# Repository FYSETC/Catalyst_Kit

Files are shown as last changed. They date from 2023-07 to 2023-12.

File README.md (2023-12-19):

# Introduction

 This is a kit for the VORON 0.2. FYSETC Voron 0. 2 Pro R1 Kit.

# Feature 

The new **Voron 0. 2 Pro R1 Kit** has a new design for the electronic part, which is easier to connect and configure, and is as close as possible to out-of-the-box use.

# BOM

[Voron 0.2 R1 Pro](https://github.com/FYSETC/FYSETC-Voron-0.2/blob/main/0.2%20R1/BOM.md)

# STL changes

### Additional STLs

Check it [here](https://github.com/FYSETC/FYSETC-Voron-0.2-Pro/tree/main/0.2%20R1/STL/ADD).

### Hotend Mount

Check it [here](https://github.com/FYSETC/FYSETC-Voron-0.2-Pro/blob/main/0.2%20R1/STL/Toolheads/Hotend_Mounts/Fan_Saver/%5Ba%5D_FS_Hotend_Mount_Dragon.stl)

### Unnecessary STLs
- Rear_Bed_Mount_Right_x1.stl
- Front_Bed_Mount_x1.stl
- Rear_Bed_Mount_Left_x1.stl
- Drag_Chain_Spacer_x1.stl
- PCB_DIN_Clip_x2.stl
- PCB_DIN_Clip_x2.stl
- Fan_Mount_Bottom_x1.stl
- VHB_DIN_Mount.STL
- VHB_DIN_Mount.STL
- Fan_Mount_Top_x1.stl
- M2_Nut_Adapter_Rotated_x5.stl

# Wiring

### R1 Pro kit

Following is our Catalyst board wiring diagram for VORON 0.2 R1 pro kit.



# Installation Guide 

### Page 190 "ELECTRONICS & WIRING"

Following the Catalyst board wiring diagram for VORON 0.2 pro R1 kit.

Check it [here](https://github.com/FYSETC/FYSETC-Voron-0.2-Pro/blob/main/0.2%20R1/Fysetc%20Voron%20V0.2%20R1%20umbilical%20Wiring.pdf).

# Firmware&OS

## CM68 OS 

<p style="color: green">
<strong>
The control board of this kit has been installed with Klipper OS and MCU Klipper firmware at the factory. And it's pre-configured.
As long as the wiring is correct, it can be used after power on.
</strong>
</p>

<p style="color: red">
<strong>
Do not perform the following steps unless you are sure you want to reinstall the firmware.
</strong>
</p>

The control board uses the CM68 core based on RK3568 as the upper computer of Klipper. Its system is compiled based on Debian 10, and the environment and plug-ins required by Klipper are pre-installed. After burning, it can be used directly.

In general, the pre-installed system can be used directly without re-flashing, unless you encounter unsolvable program problems.

The OS of CM68 (voron-02-pro):

1. Install klipper and its necessary plug-ins in the initial version (Debian10):</br>
file name: rk3568-debian10-voron02pro-mainsail.rar</br>
Download：</br>
https://drive.google.com/file/d/13Tcclv2N4jrMm01r_HPVqZ3v6CVUCk1H/view?usp=drive_link

2. bugfix (Debian10) Install klipper and its necessary plug-ins:</br>
file name: cm68-debian10-voron02pro-mainsail-20230923-154632.img</br>
Fix "vdd_cpu: ramp_delay not set" warning</br>
Download：</br>
https://drive.google.com/file/d/13Tcclv2N4jrMm01r_HPVqZ3v6CVUCk1H/view?usp=drive_link

3. 5.1 kernel, Debian11, install klipper and its necessary plug-ins:</br>
file name: cm68-debian11-voron02pro-part-20231107-1211.img</br>
Download：</br>
https://drive.google.com/file/d/1rhYSTQhsnIySWOnArb-KzfS_5ioayIdm/view?usp=drive_link</br>

4. 5.1 kernel, Debian11, install all plug-ins supported by kiauh.</br>
**file name:** cm68-debian11-voron02pro-all-20231107-1157.img</br>
**Download:** </br>
https://drive.google.com/file/d/1RwSsYh74uzc6N8ZZUWCPG4JZDjomelVW/view?usp=drive_link
Google Docs

**5 & 6 Fixed the RTL8188EUS WIFI Diver issue** </br>

5. 5.1 kernel, Debian11, install all plug-ins supported by kiauh.</br>
**file name:** cm68-debian11-voron02pro-all-20231215.rar</br>
**Download:** </br>
https://drive.google.com/file/d/1aGxkKDje69fH9lJNZlRNIsSG2d_Z3Y20/view?usp=drive_link/</br>

6. 5.1 kernel, Debian11, install klipper and its necessary plug-ins:</br>
**file name:** cm68-debian11-voron02pro-part-20231215.rar</br>
**Download:** </br>
https://drive.google.com/file/d/1jtd5bbeK2osySYbc_Y-N9HqvL0vuzt-D/view?usp=drive_link/</br>

Update steps:

1. plugin the USB3.0 A-A cable into the interface on the upper layer of the blue USB3.0 socket,
2. open the "RKDevTool_Release",
3. hold the recovery button, click the reset button, when the RKDevTool found device, release the 2 buttons
4. Click the Upgrade Firmware tab, click the Firmware button to select the firmware, and click the Upgrade button to upgrade
5. Wait for the upgrade to complete. Remember not to cut off the power or unplug the data cable during the process, otherwise the upgrade will fail or even damage the CM68.

## MCU Firmware

<p style="color: red">
<strong>
Do not perform the following steps unless you are sure you want to reinstall the firmware.
</strong>
</p>

If you know the structure of Klipper, then you should understand that the firmware of the MCU is compiled and installed by the host computer (CM68). This is the way we recommend.

Of course, you can also use other methods to burn the MCU, such as through the "STM32CubeProgrammer" on the computer, or with the help of burning tools such as STlink. These need to be studied by yourself, and our control board also provides corresponding interfaces.

The MCU model we use is STM32F401RCT6, with an external 8Mhz crystal oscillator, and uses PA11/PA12 as USB communication. The following is the MCU configuration and burning process:

1. MCU enters DFU mode:

   - Powered off the whole machine
   - Use a jumper cap to connect 3V3 and B0(boot0)
   
  
   - Power on the whole machine and wait for it to start

2. Use putty or similar SSH tools to connect to CM68 using IP or host name

    ```
    host name: voron-02-pro.local
    Username: linaro
    Password: linaro
    If you are not very familiar with linux, do not use the root user to log in. Misoperation may cause damage to the system.
    Username: root
    Password: root
    ```

3. Configure the firmware:

    - use "lsusb" to ensure the mcu enter dfu mode,

       ```
       lsusb
       ```

    - configure the firmware
    
       ```
       cd ~/klipper
       make clean
       make menuconfig
       ```

4. update the firmware and reboot

    - Compile and burn the firmware:
    
      ```
       make flash FLASH_DEVICE=0483:df11
      ```
    
    - Powered off the whole machine
    - Use a jumper cap to connect B0(boot0) and G(GND)
      

    - Power on the whole machine and wait for it to start

# Print

## Connect via Ethernet

The control board defaults to obtain IP automatically, make sure your router can provide DHCP service normally. You only need to plug in the Internet cable, and when you see the green and yellow lights on, indicates that it is connected to the network.

You have two methods to login the mainsail webpage:

### IP address
you need to go to your router to find the device named voron-02-pro, and write down the IP address
### Host name
The kit has already installed the required plug-ins, and you can access the mainsail page through the pre-set host name: voron-02-pro.local

## Connect via WiFi

- First connect the machine to your LAN via Ethernet, make sure you can log in to CM68 via SSH.
- Plug the included USB wifi into any USB interface on CATALYST board
- Use the following command checks whether the wifi module is recognized:
```
sudo ifconfig
```
- Use the following command to connect to wifi
```
sudo wifi_sta_start.sh ssid password
```
- Use the following command checks whether the wifi module is connected to your router, and get the ip address:
```
sudo ifconfig
```

# FAQ

## 1. Can't find mcu/unable to connect to mcu
Reason:
       It may be that the status of boot0 is uncertain, causing the STM32 to enter the DFU mode, resulting in the connection error.
Solution:
   - Powered off the whole machine
   - Use a jumper cap to connect B0(boot0) and G(GND)
   - Power on the whole machine and wait for it to start
## 2. Mcu firmware version too low
Reason:
The factory version of the Klipper host is the same as that of the MCU. Maybe you have clicked the update button on the mainsail webpage to update the Klipper host. As a result, the version of the host is newer than the firmware of the MCU.
Solution:
update the mcu firmware: Refer to the Firmware&OS==>MCU Firmware
## 3. Temperature error
Reason:
You may have forgotten to connect the MX3.0 16P cable, or it may not be connected firmly.
Solution:
Make sure the MX3.0 16P cable is connected and secure.
## 4. How to use the accelerometer
Refer to Klipper document: 
https://www.klipper3d.org/Resonance_Compensation.html

## 5. Wifi Connection Issues
If you are having problems with your Catalyst wifi, please fix using the following solution. 

SSH into the Catalyst, and run the following command `sudo nano /etc/network/interfaces`

Once you have run the command, add the following lines 

```
auto wlan0
iface wlan0 inet dhcp
wpa-ssid Your Network Name Here
wpa-psk Your Password Goes Here
```
example if your wifi name is fysetcwifi and password was ItRocks:
```
auto wlan0
iface wlan0 inet dhcp
wpa-ssid fysetcwifi
wpa-psk ItRocks
```

# Support
Voron community: 
https://discord.gg/voron
FYSETC Facebook group: 
https://www.facebook.com/groups/238970713918171
FYSETC Discord:
https://discord.gg/T3XcJPgr 
# Buy Link
https://www.aliexpress.us/item/3256805148633512.html

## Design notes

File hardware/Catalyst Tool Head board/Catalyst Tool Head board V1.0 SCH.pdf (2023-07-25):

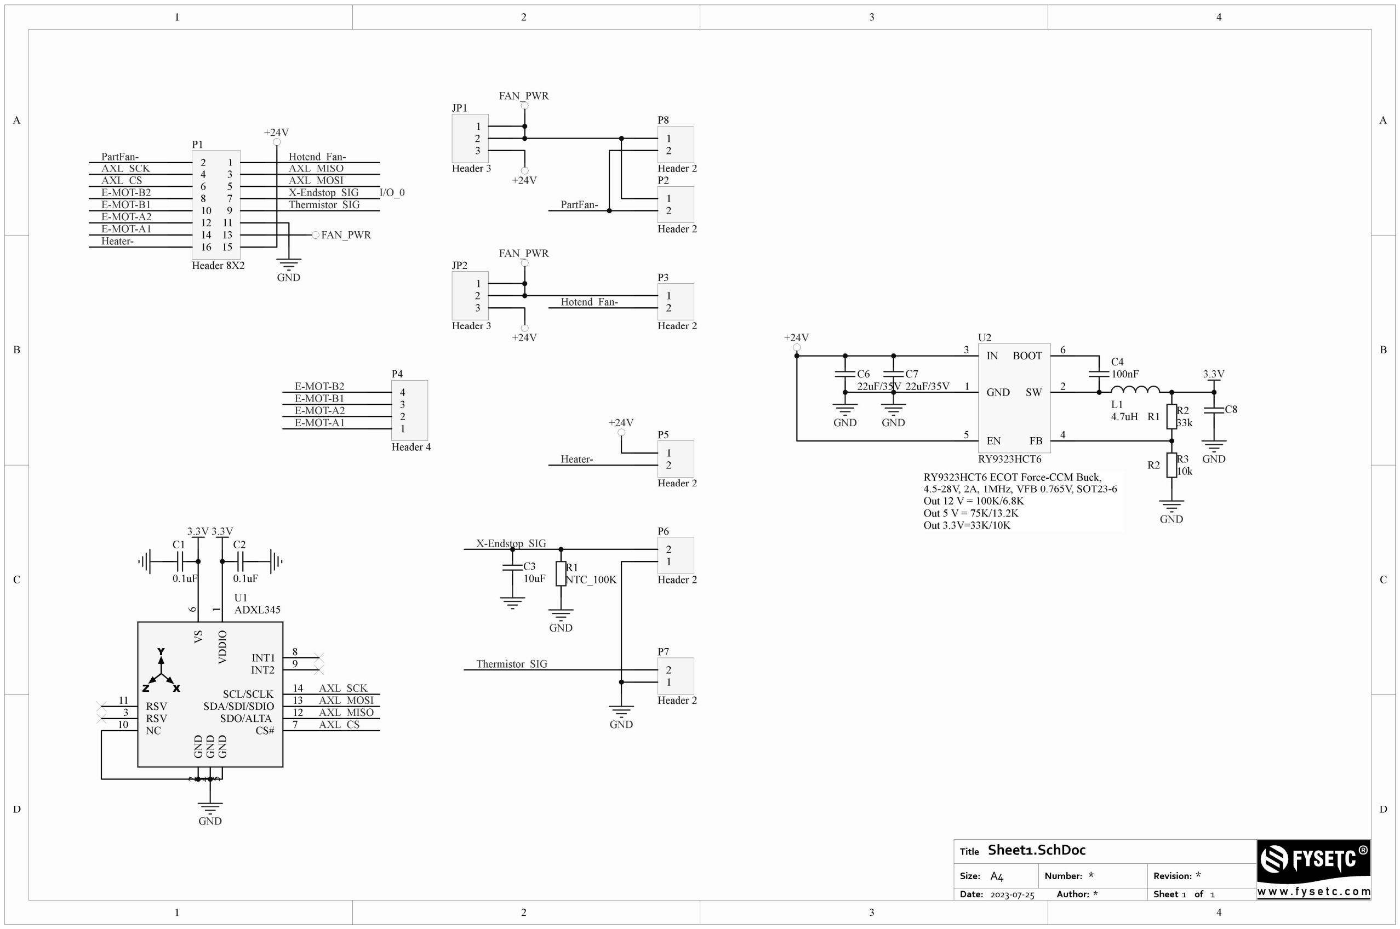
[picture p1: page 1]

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
## Sheet1.SchDoc

* | *
2023-07-25 | *

Title

Size: | Number:
Date:

Revision:
Author: | Sheet | of

A4

E-MOT-A1

E-MOT-A2

E-MOT-B1

E-MOT-B2
Thermistor_SIG

GND

+24V

Heater-

PartFan- | Hotend_Fan-
X-Endstop_SIG | I/O_0

AXL_MISO
AXL_CS | AXL_MOSI
AXL_SCK | 2 | 1
4 3
6 5
8 7
10 9
12 11
14 13
16 15

P1

Header 8X2

1

2

3

4

P4

Header 4

SDA/SDI/SDIO | 13
SDO/ALTA | 12 GND

### 2 GND

### 4 GND

## 5 VDDIO

### 1 VS

6

SCL/SCLK | 14
CS# | 7
INT1 | 8
INT2 | 9
NC 10 | RSV 3

RSV 11

ADXL345

U1

GND

3.3V
C2

0.1uF

3.3V
C1

0.1uF

AXL_MISO

AXL_MOSI

AXL_CS

AXL_SCK

E-MOT-A1

E-MOT-A2

E-MOT-B1

E-MOT-B2

1
2

P2

Header 2

Heater-

PartFan-

Hotend_Fan- | 1
| 2

P3

Header 2

1
2

P5

Header 2

+24V

1

2

P6

Header 2

FAN_PWR

1

2

P7

Header 2

Thermistor_SIG

X-Endstop_SIG

GND

R1
NTC_100K

GND

C3
10uF

+24V

C4
100nF

L1
4.7uH | R2
| 33k
| R3
| 10k

GND

C8

GND

R1

R2

C7
22uF/35V

GND
FB 4 EN 5

GND 1

IN 3

SW | 2
BOOT | 6

U2

RY9323HCT6
RY9323HCT6 ECOT Force-CCM Buck, 4.5-28V, 2A, 1MHz, VFB 0.765V, SOT23-6 Out 12 V = 100K/6.8K
Out 5 V = 75K/13.2K
Out 3.3V=33K/10K

C6
22uF/35V

GND

3.3V

1
2

P8

Header 2

FAN_PWR

1
2
3

JP2

Header 3
+24V

FAN_PWR

1
2
3

JP1

Header 3
+24V

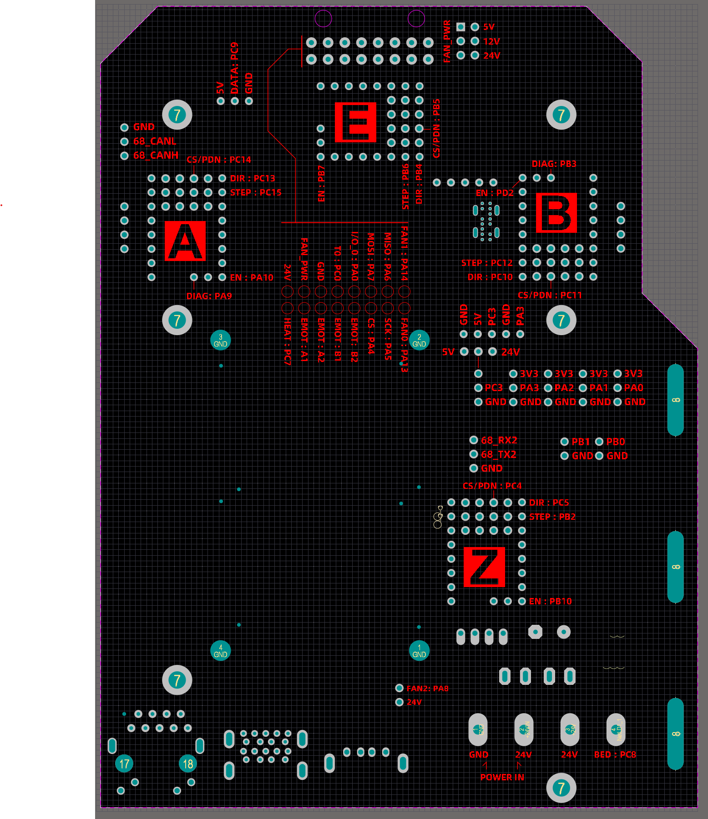
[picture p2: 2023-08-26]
CATALYST V1.0 Pinsout.png

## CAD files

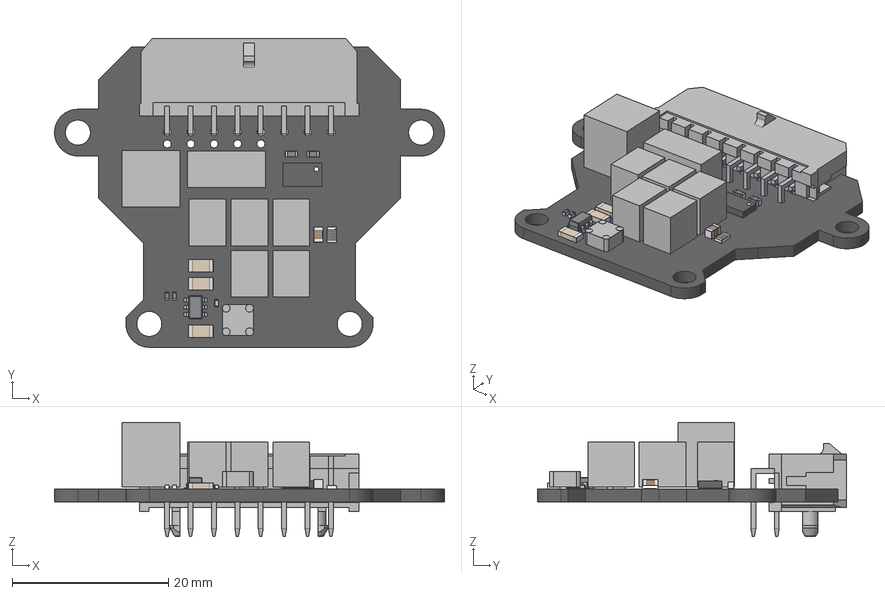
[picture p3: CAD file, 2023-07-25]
3D/Catalyst Tool Head board V1.0 3D.step
50.0 x 39.6 x 14.6 mm
Leader x 6
Mid_Body x 2
Mark x 2
Extruded x 8
C1206 x 3
RESC2012X05N(0805)
CAP0805
SW3dPS-LGA-14_Board3
SW3dPS-LGA-14_Extruded3 x 14
SW3dPS-LGA-14_Extruded5
SW3dPS-LGA-14_Extruded4
SW3dPS-LGA-14_Cylinder1
SW3dPS-LGA-14_Board2
User Library-V0603HD_K_X_F6rper_1 x 2
User Library-V0603HD_Anschl_X_FCsse_1 x 2

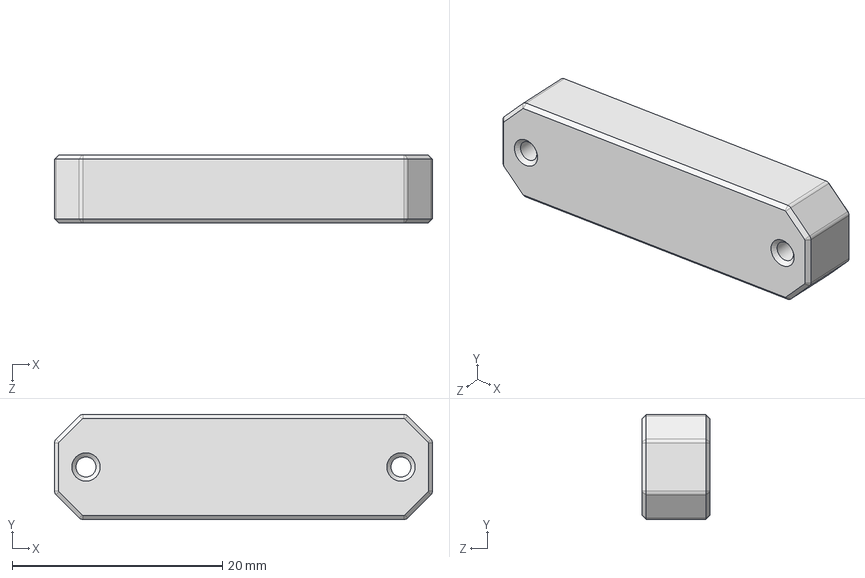
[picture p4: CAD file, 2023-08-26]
CATALYST_Mount_Separation/3D/CATALYST_Mount03_x3.STEP
36.0 x 10.0 x 6.50 mm

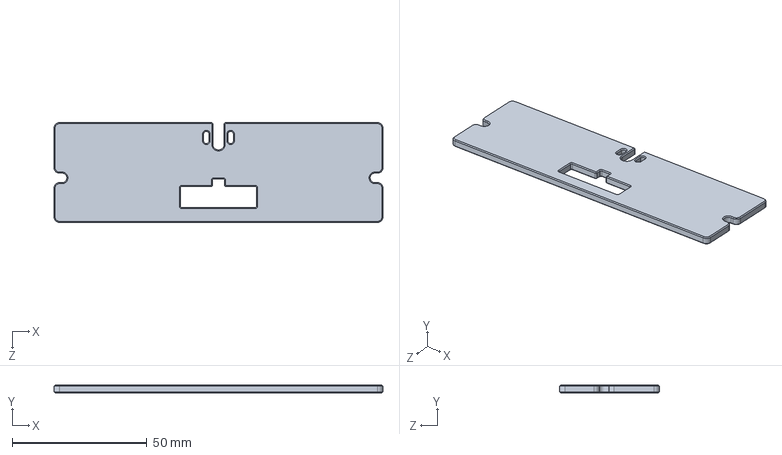
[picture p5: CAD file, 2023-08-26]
CATALYST_Mount_Separation/3D/Motor Panel_x1.STEP
122.0 x 3.00 x 37.0 mm

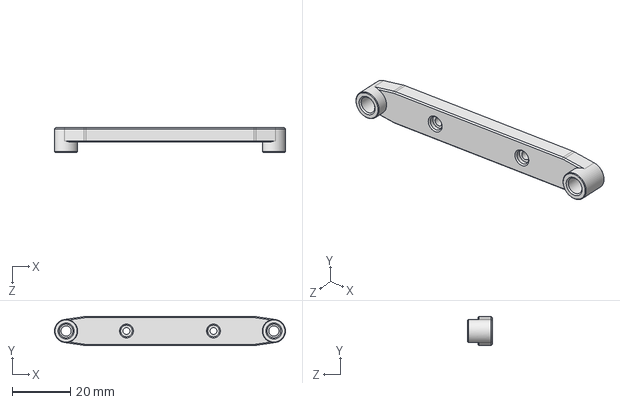
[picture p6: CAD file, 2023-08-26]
CATALYST_Mount_Separation/3D/CATALYST_Mount02_x1.STEP
79.6 x 10.0 x 8.50 mm

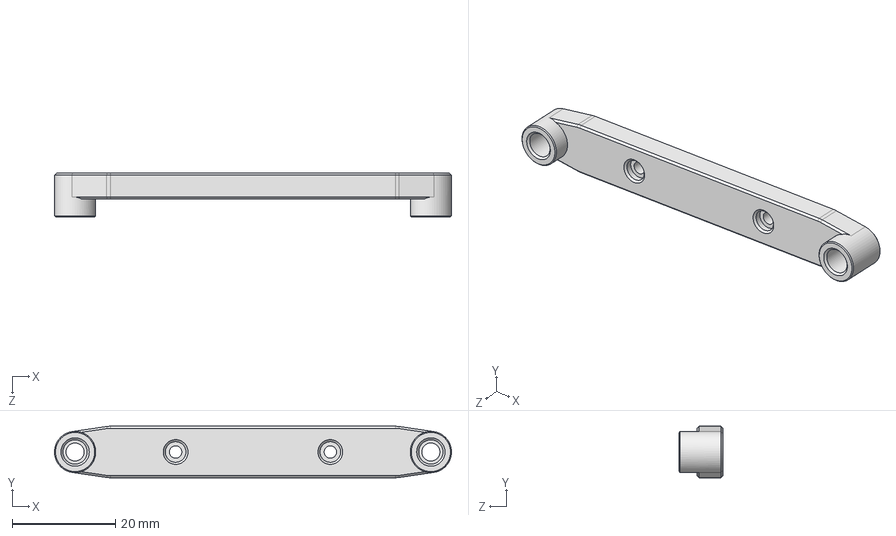
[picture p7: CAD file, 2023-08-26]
CATALYST_Mount_Separation/3D/CATALYST_Mount01_x2.STEP
77.0 x 10.0 x 8.50 mm

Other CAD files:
CATALYST_Mount_Separation/STL/CATALYST_Mount01_x2.STL
CATALYST_Mount_Separation/STL/CATALYST_Mount02_x1.STL
CATALYST_Mount_Separation/STL/CATALYST_Mount03_x3.STL
CATALYST_Mount_Separation/STL/Motor Panel_x1.STL

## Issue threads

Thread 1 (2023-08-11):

Setup board

polovi, 2023-08-11:
hi, could you upgrade the repository with some information on how to install the system and klipper, how to set jumpers for tmc2209, WiFi, or in what condition is the board sold?  From the pictures, I saw that the voron0r1 kit has at least some information and an infographic for wiring, but the separately sold board only has a link to a non-existent wiki

Closed 2023-09-09.

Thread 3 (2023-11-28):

Unable to Update OS on CM68 Board

pireybr, 2023-11-28:
I am writing to report an issue I am experiencing while trying to update the OS on my CM68 board. I have followed the procedures outlined on GitHub and sought assistance on Discord, but unfortunately, I have not been successful in completing the update.

I have attempted the update process on two different computers using the USB cable provided in the V0.2 pro R1 kit, but the issue persists.

Could you please provide guidance on resolving this matter.

Thank you for your attention.

monmono, 2024-03-13:
I have the same problem, did you solve it?

beavis69, 2024-03-13:
The only way i managed to update the os was using another linux computer.

Download and unrar this on another linux computer : https://github.com/vicharak-in/rockchip-linux-tools/blob/master/linux/Linux_Upgrade_Tool/upgrade_tool_v2.22.tar

Download one of the image provided and unrar it.

Boot the cm68 in maskrom mode (using rst + maskrom buttons).

Connect usb male/male cable between the 2 computers ( upper usb3 port on the catalyst).

Use the command :

monmono, 2024-03-14:
Thanks, I will try that.

yebo29, 2024-05-16:
Do I need to be holding the reset and maskrom buttons before powering on or does it have to be on when doing that?

yebo29, 2024-05-22:
Got it, thanks!

therealpurplemana, 2024-12-14:
Can this board update on Mac or Windows? I can't get it to detect the device to reflash.

wslotboom, 2025-01-04:
For windows users, first install adb drivers. After installation my board was detected. Drivers can be downloaded from here: https://wiki.radxa.com/Rock/windows_adb

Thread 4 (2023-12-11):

Adding Motor Drives on Catalyst Motherboard

MJ0423, 2023-12-11:
Is there simple way to connect additional motor drives?

eliwong, 2024-02-20:
You need at least 4 free IOs. Any ones not used on the board can be used for motor control, but this is not very simple.
Maybe consider connecting an external single-axis driver board with an MCU?

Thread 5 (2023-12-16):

No WIFI on Debian 11 Image

Niedze, 2023-12-16:
Kein WIFI bei beiden Debian 11 Images. Kennt jemand eine Lösung?

Fungus2k, 2024-02-02:
where did you get a Debian 11 image?

eliwong, 2024-02-20:
5 & 6 Fixed the RTL8188EUS WIFI Diver issue

5.1 kernel, Debian11, install all plug-ins supported by kiauh.
file name: cm68-debian11-voron02pro-all-20231215.rar
Download:
https://drive.google.com/file/d/1aGxkKDje69fH9lJNZlRNIsSG2d_Z3Y20/view?usp=drive_link/

5.1 kernel, Debian11, install klipper and its necessary plug-ins:
file name: cm68-debian11-voron02pro-part-20231215.rar
Download:
https://drive.google.com/file/d/1jtd5bbeK2osySYbc_Y-N9HqvL0vuzt-D/view?usp=drive_link/

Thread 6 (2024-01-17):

Board SDK

edanko, 2024-01-17:
Hello!
Please upload sdk for core board or provide working armbian configs.

Xarrax, 2024-05-21:
I'm also would like something like Armbian or atleast a more clean headless and minimal image.

beavis69, 2024-06-22:
Hello,

@eliwong : Any news about making the board SDK avalaible on cloud disk ?

edanko, 2024-07-16:
@eliwong Hello again! If you can't upload the whole SDK, at least upload device tree (dts) file.

beavis69, 2024-09-04:
Hello, SDK is finally here ! https://mega.nz/folder/uVZW0AQA#LRBYIT-3ZgAqTz407XXicw

schellek, 2024-10-13:
I built and flashed the buildroot Image but the image isn't running.
It seems like it is stuck in an bootloader or rather in the Android Debug Bridge.
Also the built image has a size of ~1.4 GB whereas the images provided by FYSETC have a size of  ~7.8 GB
Do I have to change something in the SDT or flash some other parts to get the Image running?
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

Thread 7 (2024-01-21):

Update printer.cfg

Psych0h3ad, 2024-01-21:
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

Factory test area must be erased or commented out and enable correct heater pin and fans etc...

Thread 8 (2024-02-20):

Display problem

edanko, 2024-02-20:
Hi.
Encoder usage on the display causes i2c timeout errors.
Updating to latest debian image and klipper firmware does not affect this issue.
[klippy.log.2024-02-16.zip](https://github.com/FYSETC/Catalyst_Kit/files/14344058/klippy.log.2024-02-16.zip)

DylanPW, 2024-04-22:
I've had the same issue for a long time, unfortunately recently I think the display has started becoming intermittent during printing. I did read somewhere that the display cable running over the power supply could be a contributing factor but I'm yet to test this. Will report back once I do.

niedze72, 2024-07-22:
Ich hatte das gleiche Problem,
Trennt auf der einen Seite das Kabel Leitung 5 und 6 (SDA ,SDL).
Verdrillt die Leitungen miteinander und verbinde sie wieder.
Das Problem ist danach weg.

Viel Eerfolg

I had the same problem,
On one side, separates cable lines 5 and 6 (SDA, SDL).
Twist the cables together and reconnect them.
The problem goes away after that.

Many success

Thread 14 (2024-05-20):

Catalyst board does not connect to wifi, the motor drivers are noisy - sudo: unable to resolve host voron-02-pro: Temporary failure in name resolution

CTechLite, 2024-05-20:
Hello,
1)The wifi will not work for me. I can only connect by ethernet cable
and this does not work all of the time.
2) The motor drivers are very loud and noisy. Whenever the motors are
active the tmc2209 drivers make a loud humming noise.

I have followed the directions here:
https://github.com/FYSETC/Catalyst_Kit/tree/main
but I keep getting an error message:
Send command: sudo ifconfig
error messag: sudo: unable to resolve host voron-02-pro: Temporary failure in name resolution
or
Send command: sudo nano /etc/network/interfaces
error message: sudo: unable to resolve host voron-02-pro: Temporary failure in name resolution
sudo: nano: command not found

I have upgraded firmware #5 and #6 according to directions here:
https://github.com/FYSETC/Catalyst_Kit/tree/main?tab=readme-ov-file#firmwareos
The MCU is also updated.

schellek, 2024-09-21:
I am also struggeling with the same problem.
But regarding "sudo: unable to resolve host voron-02-pro: Temporary failure in name resolution"
you can add the line 127.0.0.1 voron-02-pro to /etc/hosts and the message won't be displayed anymore

schellek, 2024-11-02:
Finally my WiFi works. Just use the command nmtui. I read in discord that the dongle only works with the USB 2.0 Port.

Leomabu, 2024-12-24:
> Finally my WiFi works. Just use the command nmtui. I read in discord that the dongle only works with the USB 2.0 Port.

Thank you!!!

I connected via ssh and used the sudo nmtui command, and it activated the printer's wifi.
After that a use this comand to configure de wifi: sudo nano /etc/network/interfaces

auto wlan0
iface wlan0 inet dhcp
wpa-ssid Your Network Name Here
wpa-psk Your Password Goes Here

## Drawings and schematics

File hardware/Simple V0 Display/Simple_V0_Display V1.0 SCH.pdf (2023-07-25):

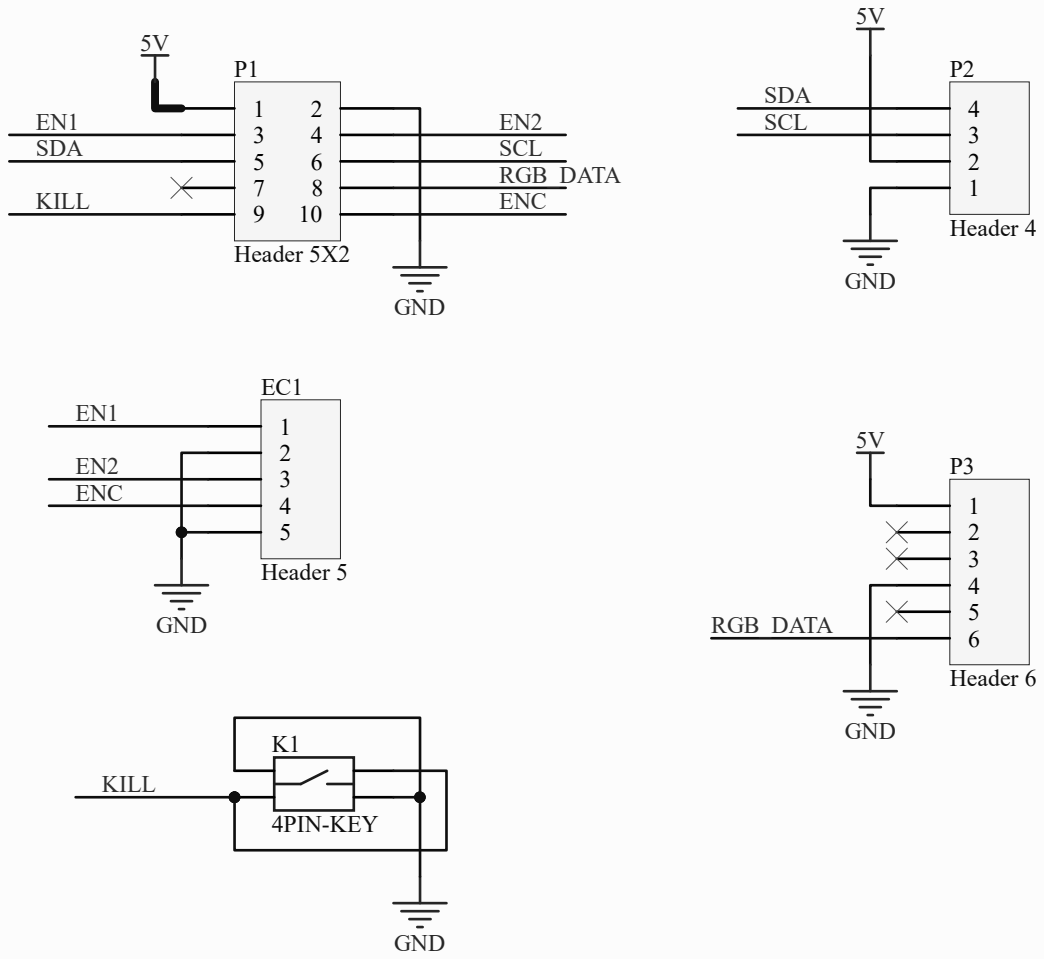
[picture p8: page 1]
Simple V0 Display .SchDoc; Title; Size:; Number:; Date:; Revision:; Author:; Sheet; Header 5X2; GND; SDA; SCL; RGB_DATA; KILL; ENC; Header 4; Header 5; SDA SCL; 4PIN-KEY; Header 6

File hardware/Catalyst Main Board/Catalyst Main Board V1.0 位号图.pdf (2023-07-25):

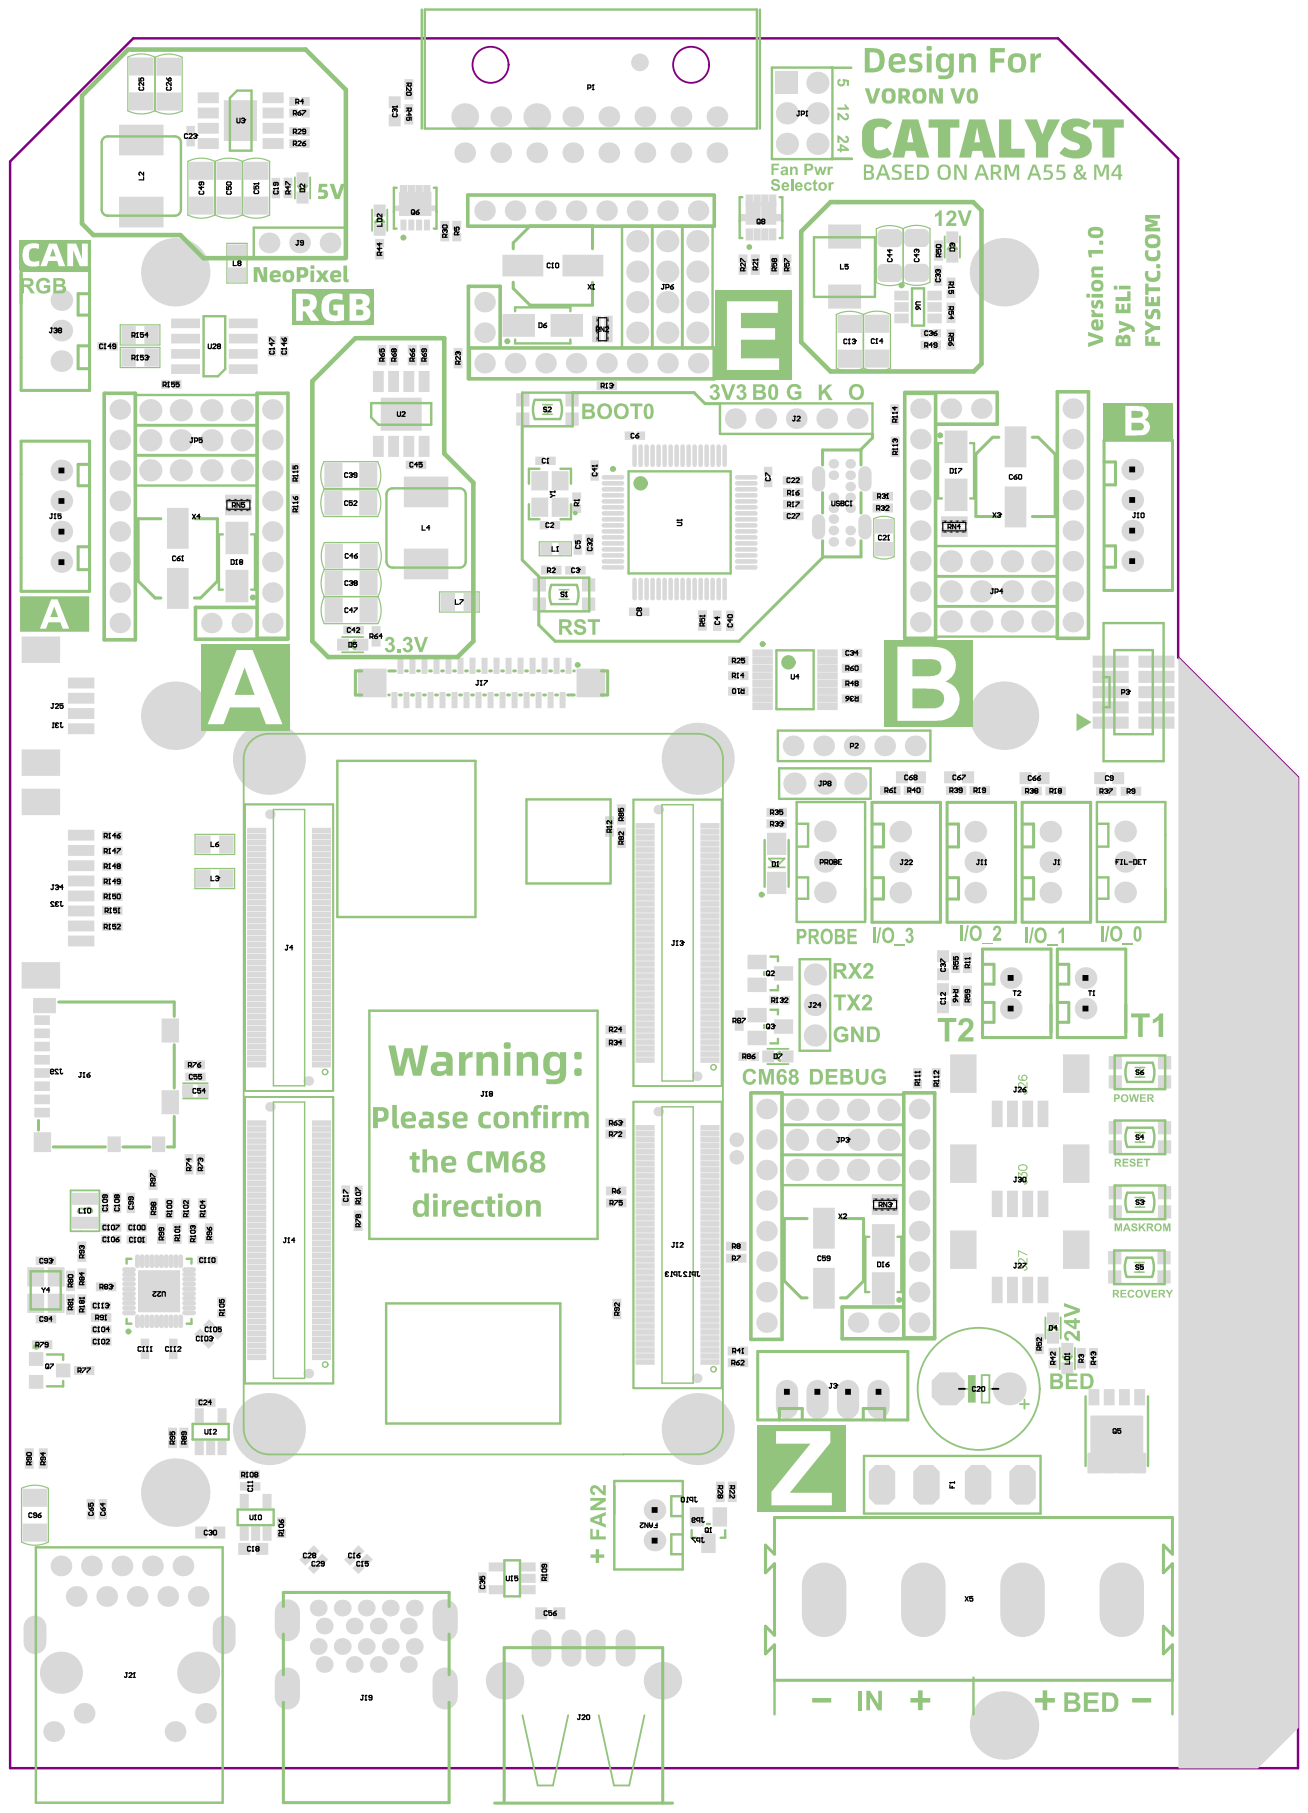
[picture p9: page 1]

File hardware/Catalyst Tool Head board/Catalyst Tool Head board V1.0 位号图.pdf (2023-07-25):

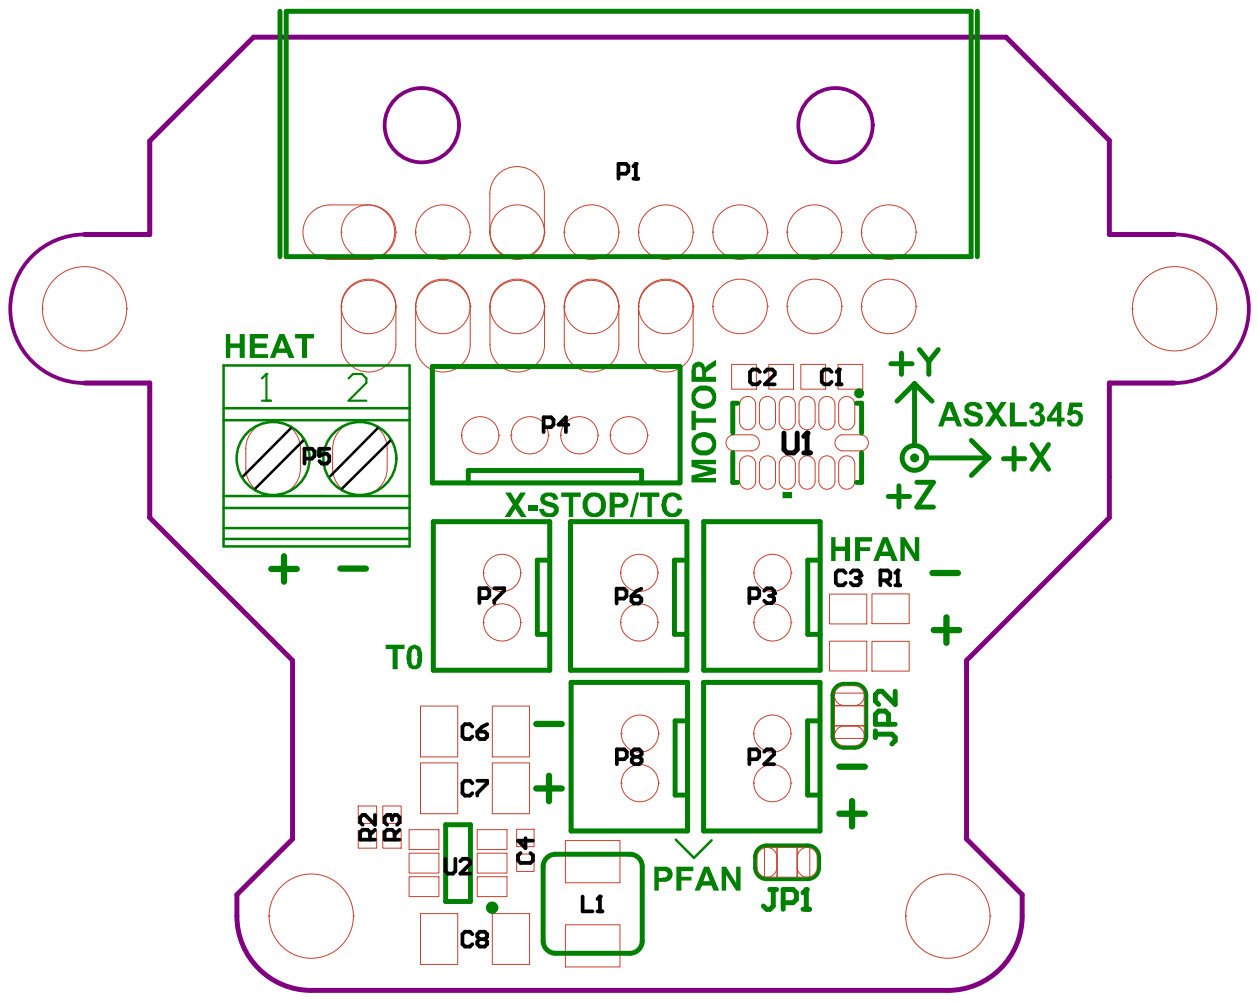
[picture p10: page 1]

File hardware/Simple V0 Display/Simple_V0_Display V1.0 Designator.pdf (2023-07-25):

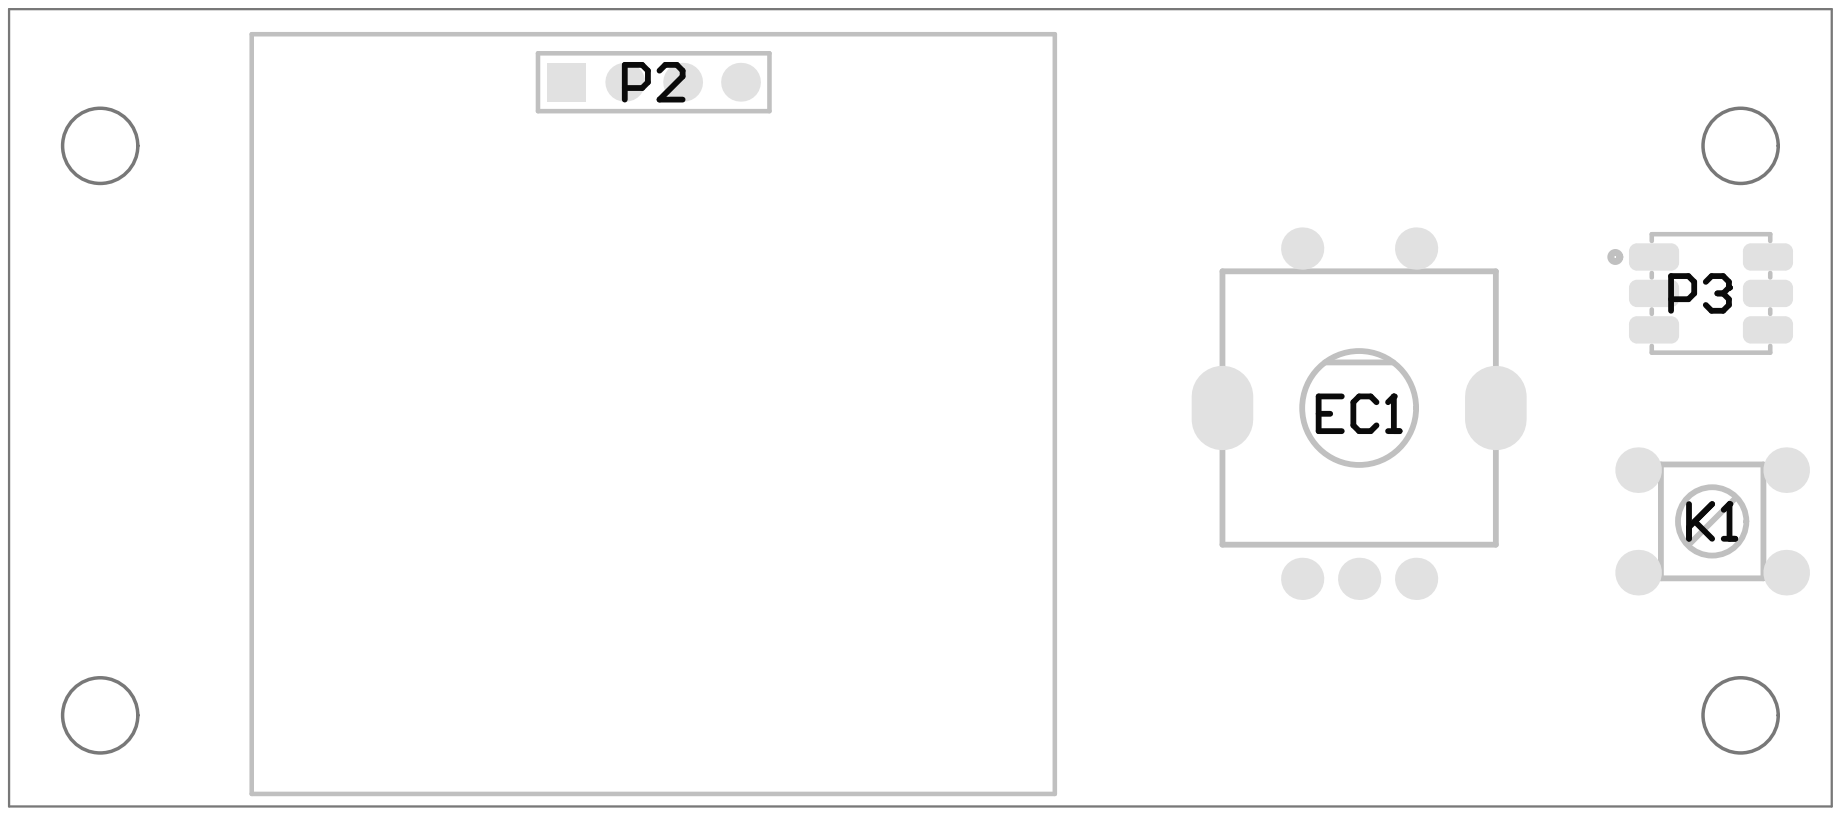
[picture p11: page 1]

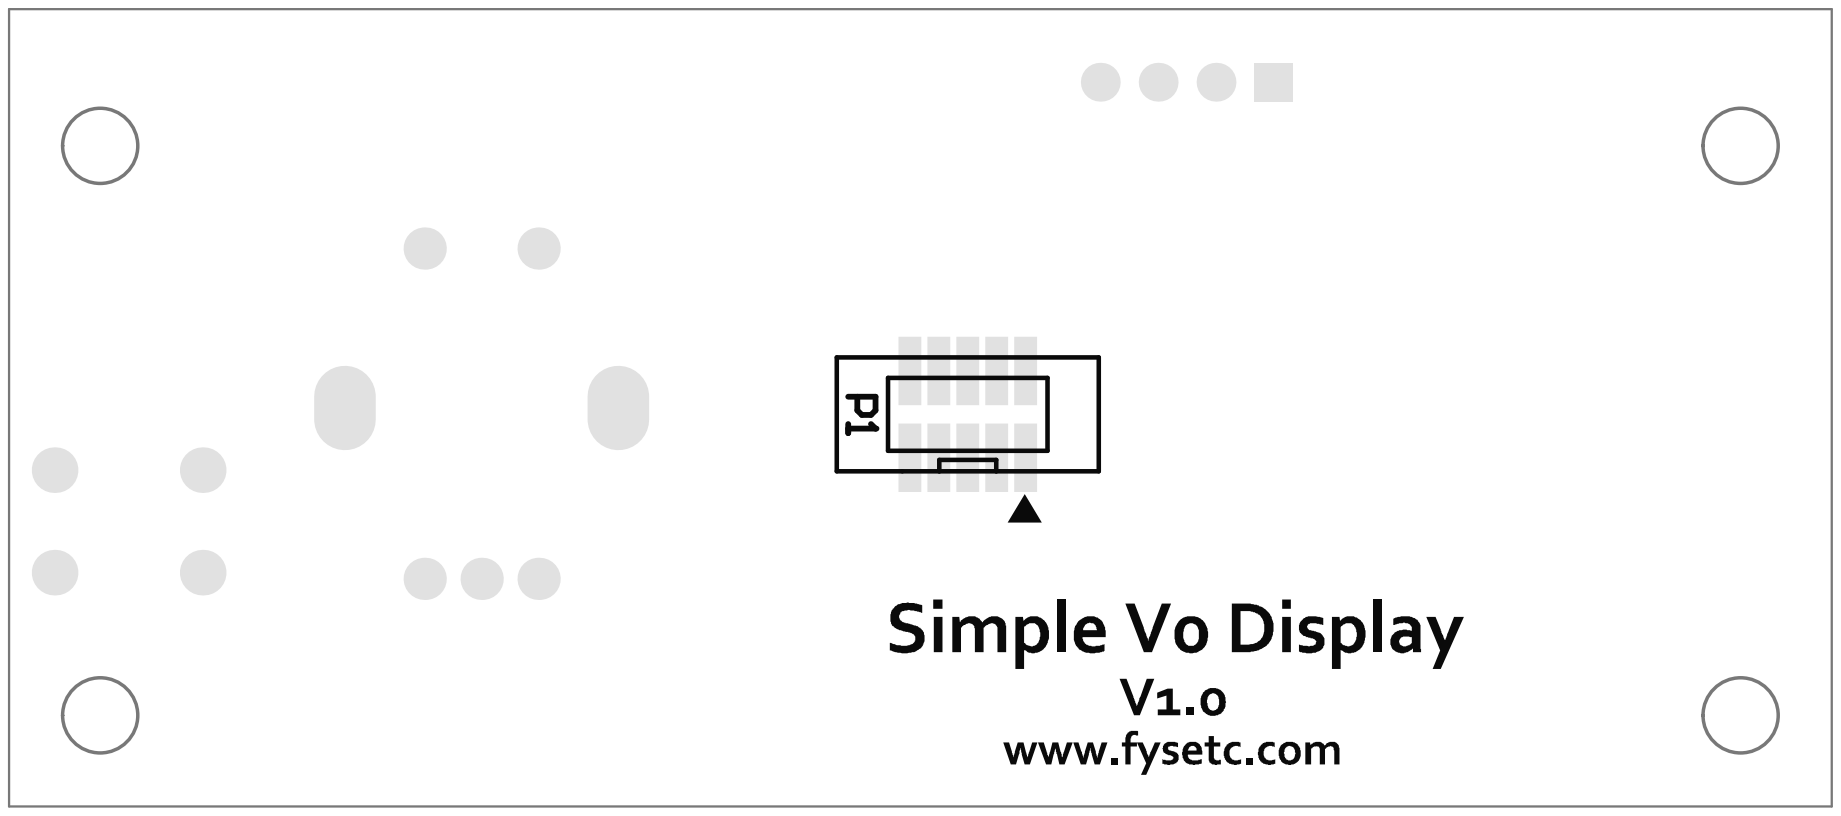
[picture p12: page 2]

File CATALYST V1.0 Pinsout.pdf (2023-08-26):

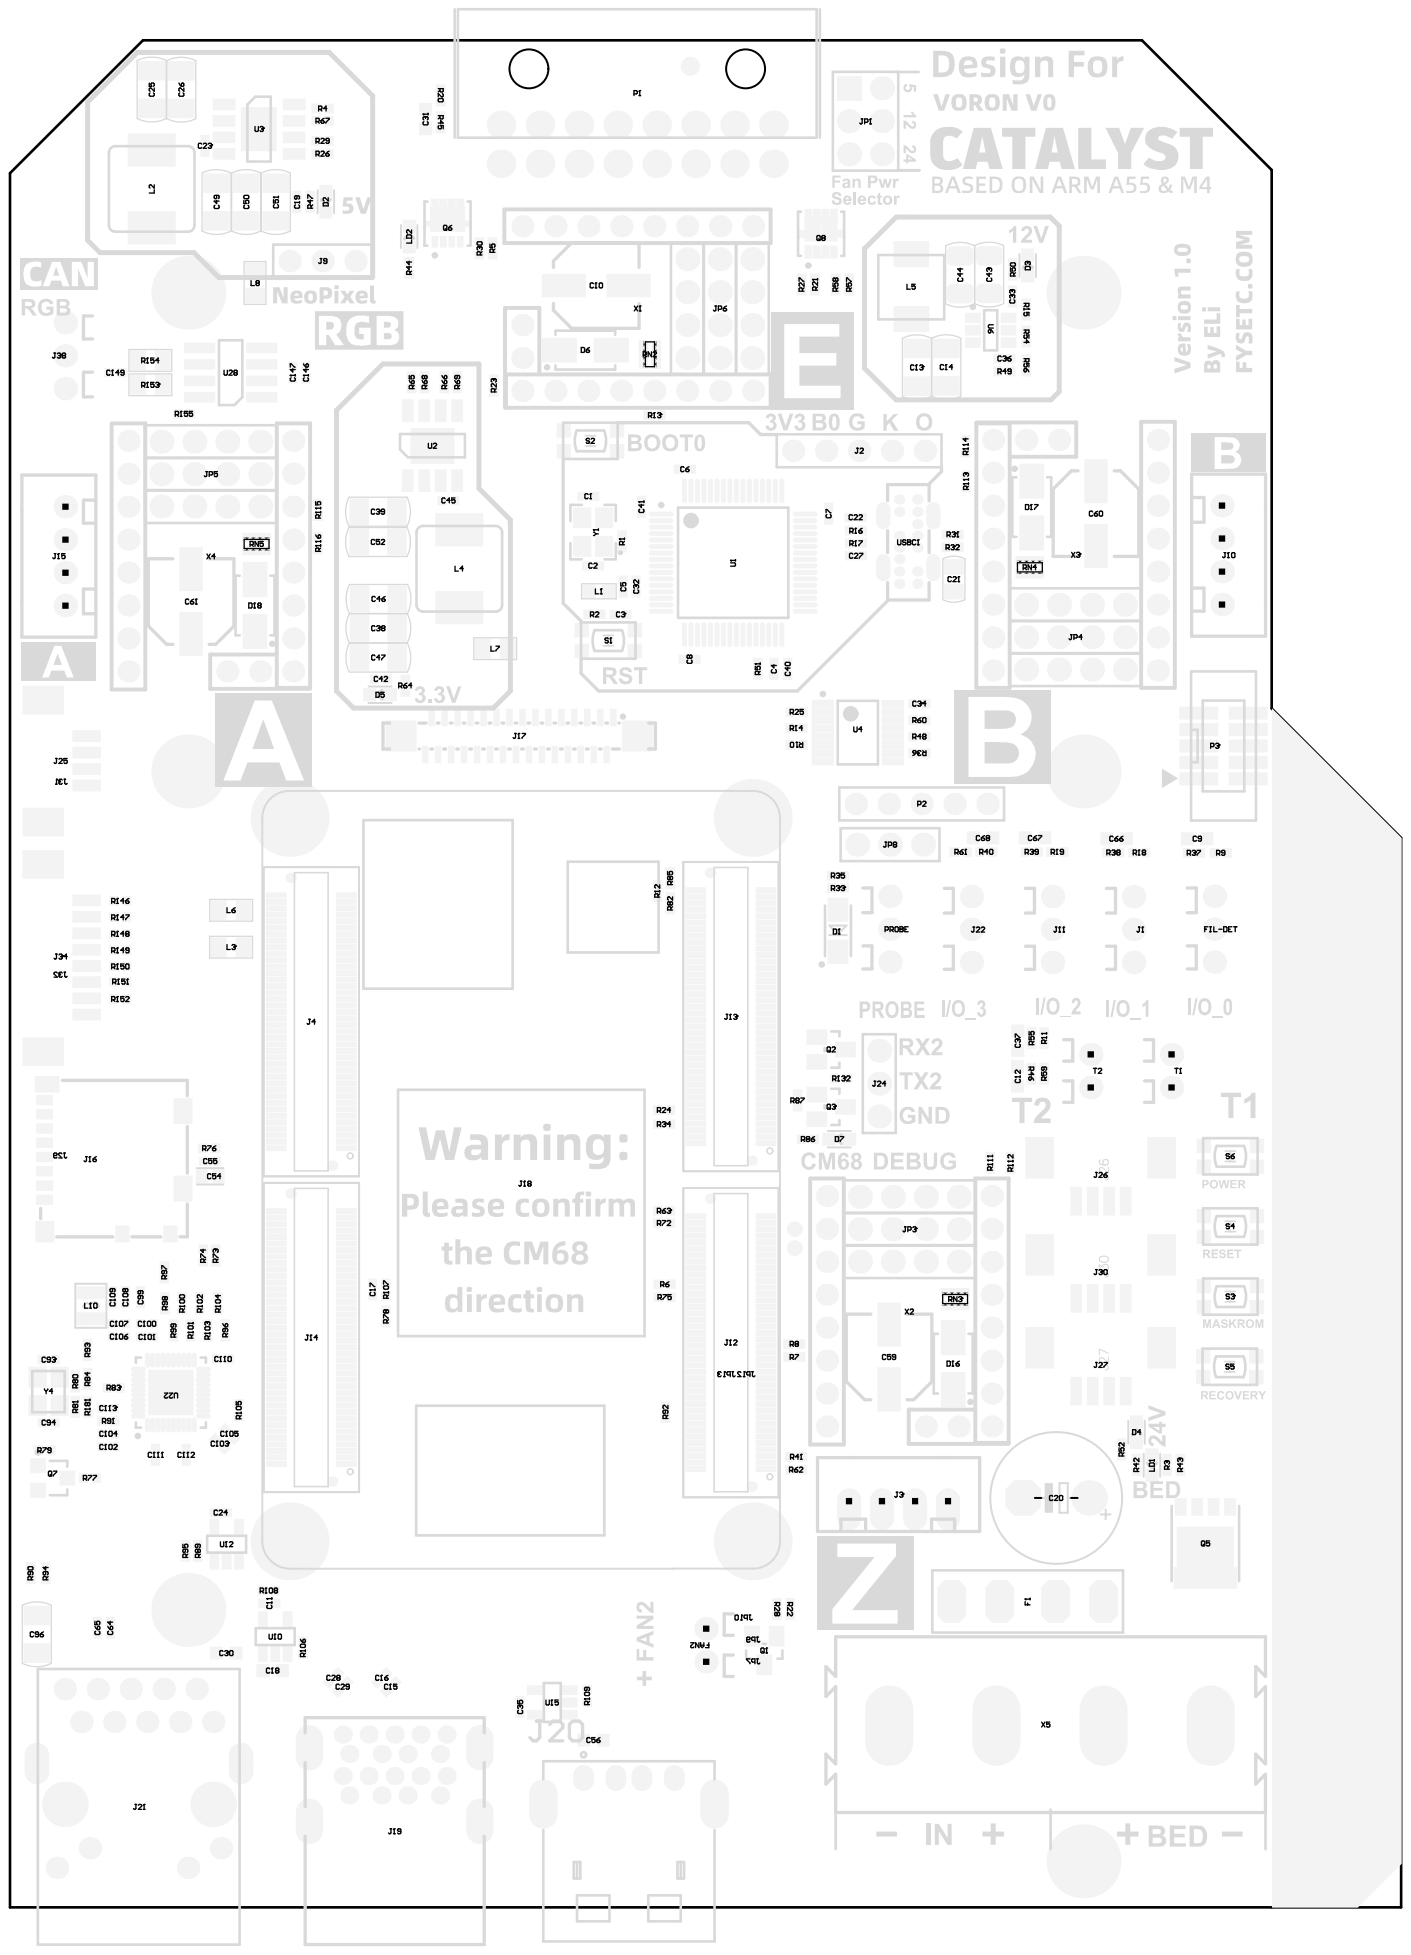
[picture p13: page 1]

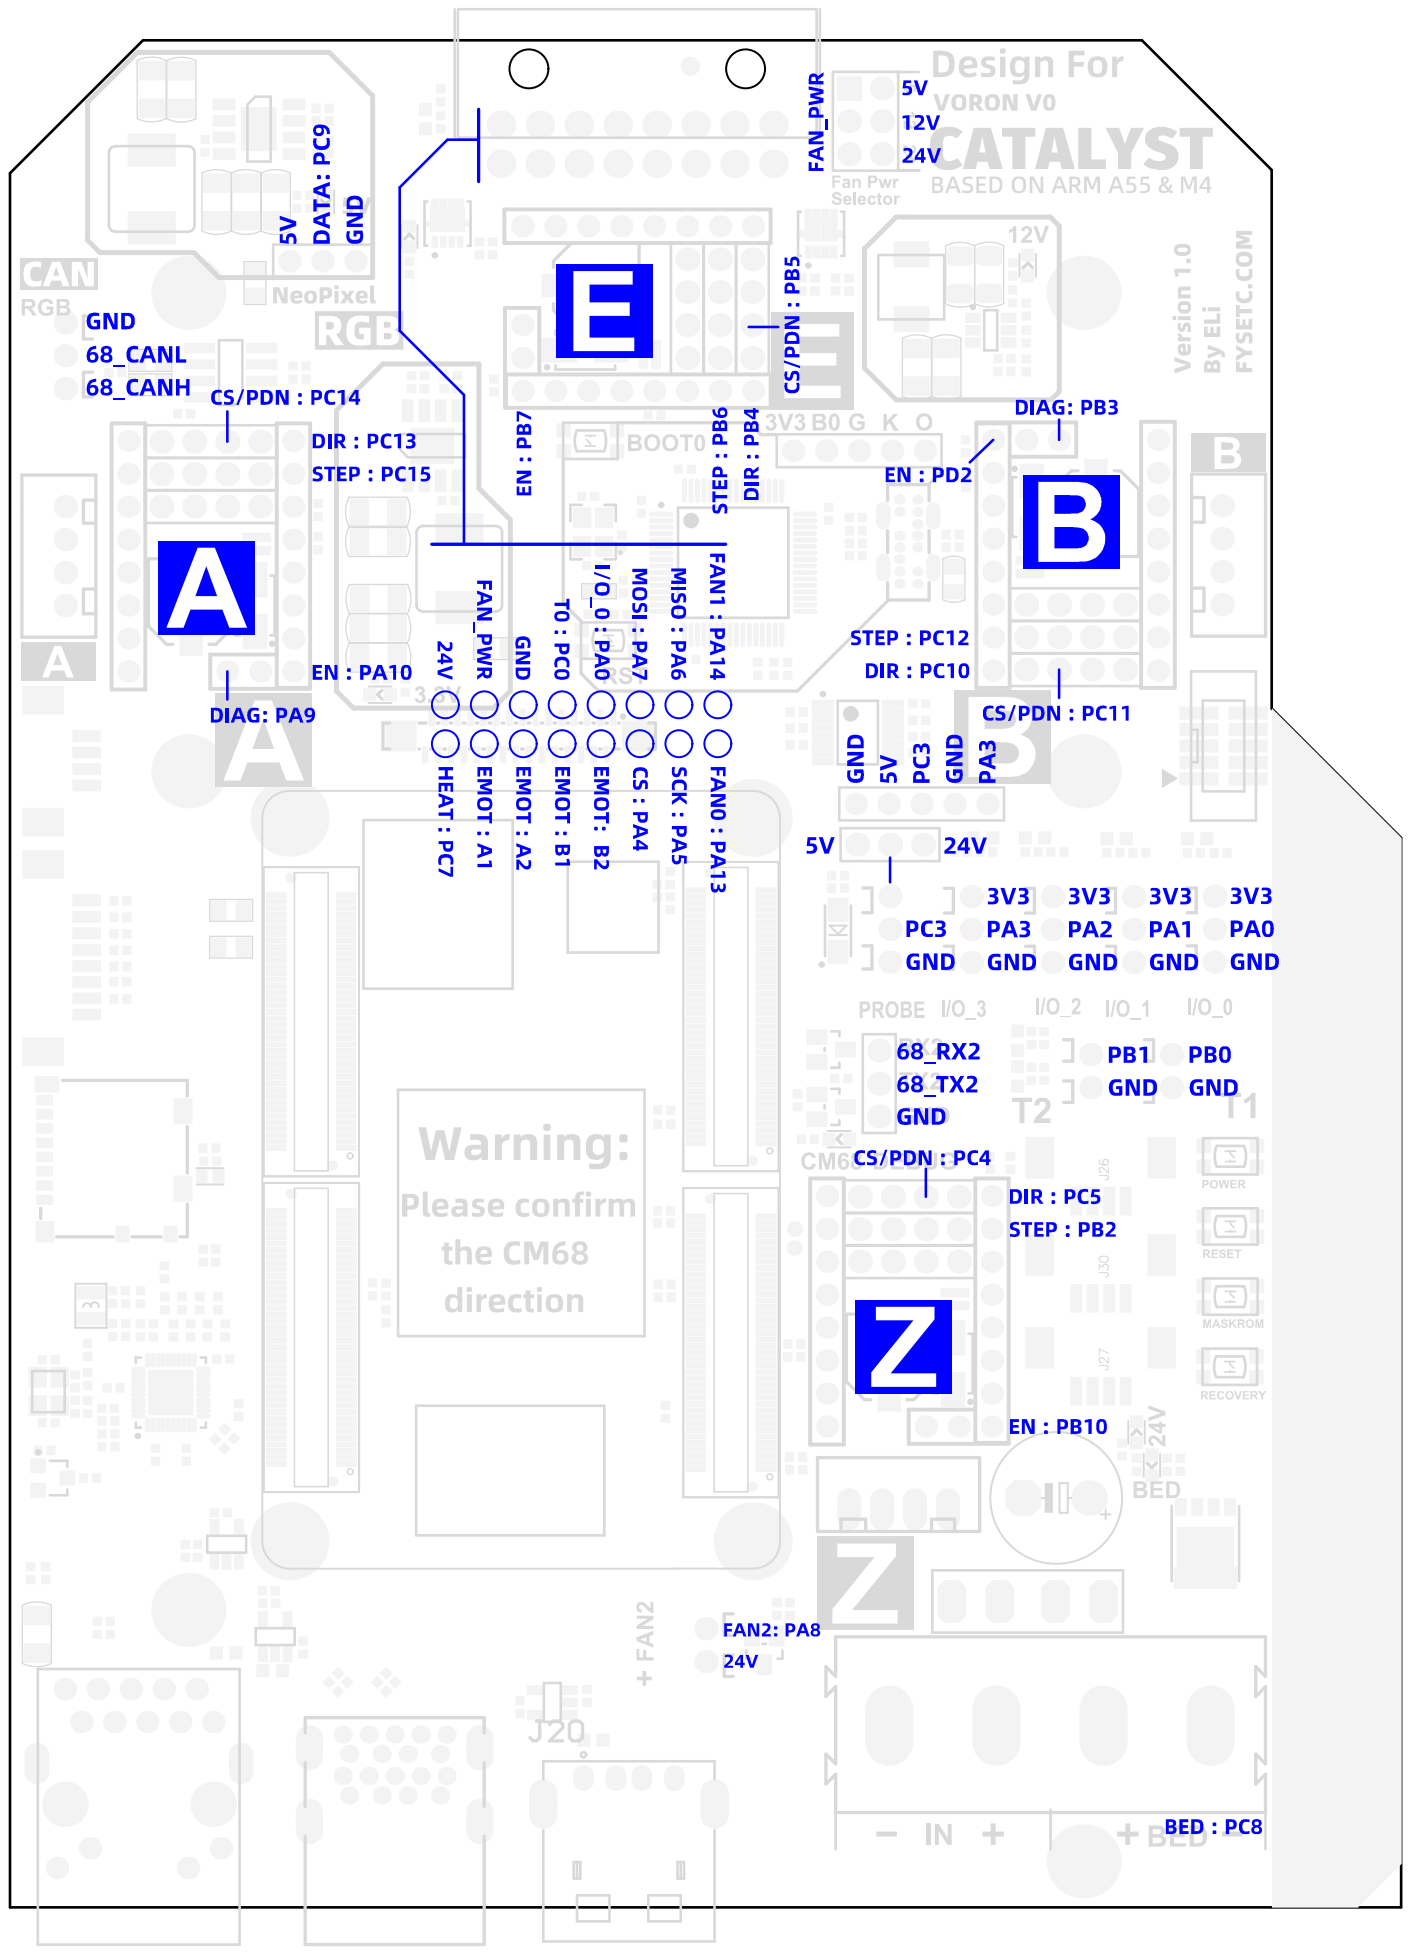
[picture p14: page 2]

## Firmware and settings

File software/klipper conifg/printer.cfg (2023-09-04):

# This file contains common pin mappings for the Fysetc CATALYST V1.0
# board. To use this config, the firmware should be compiled for the
# STM32F401 with "No bootloader" and Communication interface USB
# Set Clock Reference to ( 8  MHz crystal )

# After running "make", run the following command to flash the board:
# dfu-util -R -a 0 -s 0x08000000:leave -D out/klipper.bin

## Voron Design VORON 0.2 
## FYSETC CATALYST V1.0 config

## *** THINGS TO CHANGE/CHECK: ***
## MCU path                                                                     [mcu] section
## Z and Extruder motor currents                                                [tmc2209 stepper_*] sections. Uncomment the stepper motor you have
## Full steps per rotation for Extruder                                         [extruder] section
## Thermistor types                                                             [extruder] and [heater_bed] sections - See https://www.klipper3d.org/Config_Reference.html#common-thermistors for common thermistor types
## Extruder motor currents                                                      [extruder] section
## PID tune                                                                     [extruder] and [heater_bed] sections
## Fine tune E steps                                                            [extruder] section

## For more info                                                                check https://docs.vorondesign.com/build/startup/#v0
# See docs/Config_Reference.md for a description of parameters.

[include mainsail.cfg]

[mcu]
#####################################################################
# Obtain definition by "ls -l /dev/serial/by-id/"
#####################################################################
serial: /dev/serial/by-path/platform-fd840000.usb-usb-0:1:1.0
#restart_method: command


[printer]
kinematics: corexy
max_velocity: 200
max_accel: 3000
max_accel_to_decel: 3000
max_z_velocity: 15
max_z_accel: 45
square_corner_velocity: 6.0

#####################################################################
#      X/Y Stepper Settings   X=B   Y=A
#####################################################################

[stepper_x]
step_pin: PC12
## Refer to https://docs.vorondesign.com/build/startup/#v0
dir_pin: !PC10                                                      # Check motor direction in link above. If inverted, remove ! before PC13
enable_pin: !PD2
rotation_distance: 40
microsteps: 32
full_steps_per_rotation: 200                                        # Set to 400 for 0.9 degree stepper motor, 200 is for 1.8 degree stepper motors
#endstop_pin: ^PA3
endstop_pin: tmc2209_stepper_x:virtual_endstop
position_endstop: 120
position_max: 120
homing_speed: 40                                                    # for sensorless homing it is recommended not to go above 40mm/s   
homing_retract_dist: 0
homing_positive_dir: true

[tmc2209 stepper_x]
uart_pin: PC11
interpolate: False
run_current: 0.7
hold_current: 0.4
sense_resistor: 0.110
stealthchop_threshold: 0                                            # Set to 999999 to turn stealthchop on, and 0 to use spreadcycle
diag_pin: PB3                                                       # NO NEED TO JUMP 
driver_SGTHRS: 100                                                  # this is set to 255 which is the MAX sensitivity for sensorless homing, you will need to tune this later


[stepper_y]
step_pin: PC15
## Refer to https://docs.vorondesign.com/build/startup/#v0
dir_pin: !PC13                                                       # Check motor direction in link above. If inverted, remove ! before PC1
enable_pin: !PA10
rotation_distance: 40
microsteps: 32
full_steps_per_rotation: 200                                        # Set to 400 for 0.9�?degree stepper motor, 200 is for 1.8�?stepper motors
#endstop_pin: ^PA2
endstop_pin: tmc2209_stepper_y:virtual_endstop
position_endstop: 120
position_max: 120
homing_speed: 40                                                    # for sensorless homing it is recommended not to go above 40mm/s   
homing_retract_dist: 0
homing_positive_dir: true

[tmc2209 stepper_y]
uart_pin: PC14
interpolate: False
run_current: 0.7
hold_current: 0.4
sense_resistor: 0.110
stealthchop_threshold: 0                                            # Set to 999999 to turn stealthchop on, and 0 to use spreadcycle
diag_pin: ^PA9                                                      # NO NEED TO JUMP  
driver_SGTHRS: 100                                                  # this is set to 255 which is the MAX sensitivity for sensorless homing, you will need to tune this later


#####################################################################
#   Z Stepper Settings
#####################################################################

[stepper_z]
step_pin: PB2
dir_pin: PC5	                                                    # Remove the ! before PB8 if motor direction is inverted.
enable_pin: !PB10
rotation_distance: 8                                                # For T8x8 lead screw
#rotation_distance: 2                                               # For T8x2 lead screw
microsteps: 32
endstop_pin: ^PA3
position_endstop: 120
position_max: 120
position_min: -1.5
homing_speed: 20
second_homing_speed: 5.0
homing_retract_dist: 5.0

[tmc2209 stepper_z]
uart_pin: PC4
#tx_pin: PA2
#uart_address: 2
interpolate: False
# For FYSETC 42HSC1404B-200N8
run_current: 0.3
hold_current: 0.05
sense_resistor: 0.110
stealthchop_threshold: 0                                             # Set to 999999 to turn stealthchop on, and 0 to use spreadcycle

#####################################################################
#   Extruder
#####################################################################

[extruder]
step_pin: PB6
dir_pin: PB4	                # Add ! if moving opposite direction
enable_pin: !PB7
full_steps_per_rotation: 200    # Set to 200 for 1.8 degree motor, set to 400 for 0.9 degree stepper motor
rotation_distance: 22.23        # See calibrating rotation_distance on extruders doc
gear_ratio: 50:10               # For Mini Afterburner
microsteps: 32
nozzle_diameter: 0.400
filament_diameter: 1.750
heater_pin: PC7
## Check what thermistor type you have. See https://www.klipper3d.org/Config_Reference.html#common-thermistors for common thermistor types.
## Use "Generic 3950" for NTC 100k 3950 thermistors
sensor_type: Generic 3950
sensor_pin: PC0
control: pid            # Do PID calibration
pid_Kp: 28.182
pid_Ki: 1.978
pid_Kd: 100.397
min_temp: 0
max_temp: 270
min_extrude_temp: 170
max_extrude_only_distance: 150
max_extrude_cross_section: 1.5
pressure_advance: 0.02   # See tuning pressure advance doc
pressure_advance_smooth_time: 0.040

[tmc2209 extruder]
uart_pin: PB5
#tx_pin: PA2
#uart_address: 3
interpolate: False
run_current: 0.7
sense_resistor: 0.110
stealthchop_threshold: 0                                            # Set to 0 for spreadcycle, avoid using stealthchop on extruder


#####################################################################
#   Filament switch sensor
#####################################################################

[filament_switch_sensor my_sensor]
pause_on_runout: True
#   When set to True, a PAUSE will execute immediately after a runout
#   is detected. Note that if pause_on_runout is False and the
#   runout_gcode is omitted then runout detection is disabled. Default
#   is True.
runout_gcode: M300
#   A list of G-Code commands to execute after a filament runout is
#   detected. See docs/Command_Templates.md for G-Code format. If
#   pause_on_runout is set to True this G-Code will run after the
#   PAUSE is complete. The default is not to run any G-Code commands.
#insert_gcode:
#   A list of G-Code commands to execute after a filament insert is
#   detected. See docs/Command_Templates.md for G-Code format. The
#   default is not to run any G-Code commands, which disables insert
#   detection.
event_delay: 3.0
#   The minimum amount of time in seconds to delay between events.
#   Events triggered during this time period will be silently
#   ignored. The default is 3 seconds.
#pause_delay: 0.5
#   The amount of time to delay, in seconds, between the pause command
#   dispatch and execution of the runout_gcode. It may be useful to
#   increase this delay if OctoPrint exhibits strange pause behavior.
#   Default is 0.5 seconds.
switch_pin: ^PA2
#   The pin on which the switch is connected. This parameter must be
#   provided.



#####################################################################
#   Bed Heater
#####################################################################
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

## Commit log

2023-07-25 update file
    [Catalyst Tool Head board V1.0 3D.step, printer.cfg]
2023-08-26 Upload CATALYST_Mount
    Upload CATALYST_Mount
    [CATALYST_Mount01_x2.STEP, CATALYST_Mount01_x2.STL, CATALYST_Mount02_x1.STEP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]
2023-09-04 Update printer.cfg
    Updated to represent the correct clock reference of 8 Mhz
    [printer.cfg]
2023-09-04 Update printer.cfg
    Updated Pressure Advance setting - PLEASE STILL DO A PA CALIBRATION, but this now should be closer to the real setting.
    [printer.cfg]
2023-12-03 Added pictures to the readme.md
    Added pictures to clarify the STM32 flashing process.
